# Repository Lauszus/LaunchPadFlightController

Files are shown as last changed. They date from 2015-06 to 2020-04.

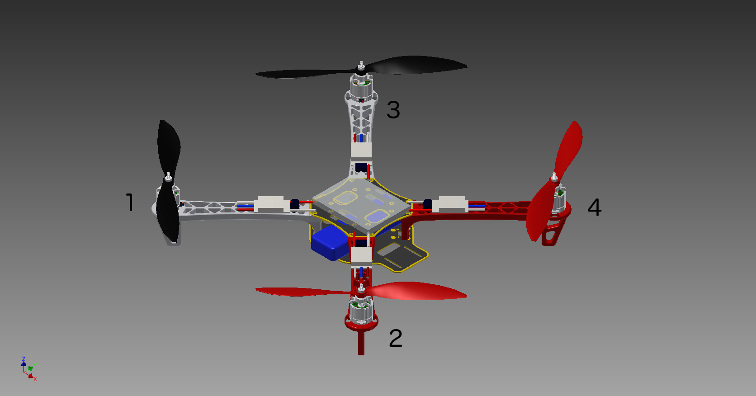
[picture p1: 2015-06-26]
docs/CD-ROM/3D_Model/Renderings/Quad_3d_overview.png

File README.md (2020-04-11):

# LaunchPad Flight Controller
#### Developed by Kristian Sloth Lauszus, 2015-2020
_________


This is a flight controller used for a quadcopter in X-configuration.

It is written for the [Tiva C Series TM4C123G LaunchPad](http://www.ti.com/tool/EK-TM4C123GXL) running at 80 MHz.

More information can be found at the following blog posts: <http://blog.tkjelectronics.dk/2015/01/launchpad-flight-controller> and <http://blog.tkjelectronics.dk/2015/08/bachelors-thesis-launchpad-flight-controller>.

# Video demonstrations

Some video demonstrations of the flight controller can be seen at my [YouTube channel](https://www.youtube.com/playlist?list=PLRBI0ZWd8RfBnD1IZzrBdREjrzRAjWMqg).



# Report

The report I wrote for my Bachelor's thesis can be found in the [docs](docs) folder. The 3D model and Matlab code can be found in there as well.

# Features

* Rate mode, self level mode, heading hold and altitude hold
    - __AUX1:__ Use 3-POS switch for self level and heading hold. At first position both are off, at second position self level is on and at third position both are on
    - __AUX2:__ Use a 3-POS switch for altitude hold. Note that self level mode must be activated for altitude hold to work! At first position altitude hold is turned off, at second position altitude hold will use the distance measured using the sonar and/or LIDAR-Lite v3 and at the third position altitude hold will be using the altitude estimated using the barometer and accelerometer
* Store PID values, calibration values etc. in EEPROM
* Gyro, accelerometer & magnetometer calibration routine
    - Gyro is calibrated at startup
    - Accelerometer and magnetometer calibration routine can be activated in the code or by using the Android app
    - The magnetometer turns on the Blue LED while calibrating
        + Rotate flight controller slowly along all three axis
* Arm/disarm using rudder
* Status LEDs
* Supports CPPM receivers
* Gyro & accelerometer (MPU-6500 or MPU-9250)
* Magnetometer (HMC5883L or AK8963 (inside MPU-9250))
* Barometer (BMP180)
* Ultrasound sensor aka sonar (HC-SR04)
* [LIDAR-Lite v3](https://buy.garmin.com/en-US/US/p/557294)
    - Connect a 680 µF electrolytic capacitor from 5V to GND
* Optical flow sensor (ADNS3080)
* [Android application](https://github.com/Lauszus/LaunchPadFlightControllerAndroid)
* OneShot125 ESC support
* Buzzer feedback

# Current setup

* Motors: Dualsky 980kv
* ESC's: [Hobby King 20A ESC 3A UBEC (F-20A)](http://hobbyking.com/hobbyking/store/uh_viewItem.asp?idProduct=37253) - flashed with SimonK bs_nfet with OneShot125 and COMP_PWM = 1
* Propellers: 10x4.5
* Frame: [Hobby King Q450 V3 Glass Fiber Quadcopter Frame 450mm](http://hobbyking.com/hobbyking/store/__49725__Q450_V3_Glass_Fiber_Quadcopter_Frame_450mm_Integrated_PCB_Version.html)
* LiPo: [Turnigy 3300mAh 3S 30C Lipo Pack](http://hobbyking.com/hobbyking/store/uh_viewItem.asp?idProduct=35870)
* RX: [OrangeRX R615X](http://www.hobbyking.com/hobbyking/store/__46632__OrangeRx_R615X_Spektrum_JR_DSM2_DSMX_Compatible_6Ch_2_4GHz_Receiver_w_CPPM.html)
* TX: [Turnigy 9XR](http://www.hobbyking.com/hobbyking/store/__31544__Turnigy_9XR_Transmitter_Mode_2_No_Module_.html) flashed with OpenTX
* TX module: [OrangeRX 2.4GHz transmitter module](http://hobbyking.com/hobbyking/store/__24656__OrangeRX_DSMX_DSM2_2_4Ghz_Transmitter_Module_JR_Turnigy_compatible_.html)

# Pinout

| Pin  | Connection | Hardware peripheral |
|---|---|---|
| PA0  | UART RX | U0RX (UART0 RX) |
| PA1  | UART TX | U0TX (UART0 TX) |
| PA2  | SPI CLK | SSI0CLK |
| PA3  | SPI SS | SSI0Fss |
| PA4  | SPI MISO | SSI0Rx |
| PA5  | SPI MOSI | SSI0Tx |
| PA6  | SCL | I2C1SCL |
| PA7  | SDA | I2C1SDA |
| PB0* | Bluetooth RX | U1RX (UART1 RX) |
| PB1* | Bluetooth TX | U1TX (UART1 TX) |
| PB4  | Motor 3 | M0PWM2 |
| PB5  | Motor 4 | M0PWM3 |
| PB6  | Motor 1 | M0PWM0 |
| PB7  | Motor 2 | M0PWM1 |
| PC5  | Sonar echo | WTimer0B (WT0CCP1) |
| PC6  | CPPM input | WTimer1A (WT1CCP0) |
| PD2  | Buzzer | |
| PE0  | Sonar trigger | |
| PE1  | ADNS3080 reset | |
| PE2  |  MPU-6500/MPU-9250 INT  | |
| PE3  | HMC5883L DRDY | |
| PF0  | Switch 1 | |
| PF1  | Red LED | |
| PF2  | Blue LED | |
| PF3  | Green LED | |
| PF4  | Switch 2 | |

\* UART1 is connected to an HC-06 Bluetooth module running at a baudrate of 115200. __Not 5V tolerant!__, so make sure your Bluetooth module outputs 3.3 voltage level or use a logic level converter.

Furthermore WTimer1B is used to turn off motors if the connection to the RX is lost. SysTick counter is used for time basic time keeping functionality.

The MPU-6500/MPU-9250, HMC5883L, BMP180 and LIDAR-Lite v3 are connected via I<sup>2</sup>C if they are used.

All pins are defined in [src/Config.h](src/Config.h) and can be overriden by creating a file called "Config_custom.h" in the [src](src) directory allowing you to redefine the values.

# Notes

The motor layout follows the Naze32 in x-configuration i.e. motor 1 is bottom right, motor 2 is top right, motor 3 is bottom left and motor 4 is top left when looking from the back. Motor 1 and 4 should be spinning clockwise and motor 2 and 3 should be spinning counterclockwise.

Make sure that roll increases when tilting quadcopter to the right, pitch increases when pitching quadcopter upward and yaw increases when rotation quadcopter clockwise. This can be displayed using the graph menu in the [Android application](https://github.com/Lauszus/LaunchPadFlightControllerAndroid).

The flight controller is armed by having the throttle low and the rudder to the right. The flight controller is disarmed again by having the throttle low and the rudder to the left.

## Initial setup

1. Locate the line ```#define ONESHOT125 1``` in [PPM.c](src/PPM.c) and set line to 0 if your ESCs does not support OneShot125, if you are in doubt, then set the value to 0.
2. Configure the orientation of the MPU-9250/6500 and HMC5883L, so they corresponds to your setup. This is done inside ```mpu6500BoardOrientation``` and ```hmc5883lBoardOrientation``` in [MPU6500.c](src/MPU6500.c) and [HMC5883L.c](src/HMC5883L.c) respectively.
    * The x-axis should be facing forward, the y-axis should be facing to the right and the z-axis should be facing downward. Typically the axis is indicated on the breakout board for the sensor.

### Calibrating the ESCs

__WARNING:__ Take propellers OFF when testing and calibrating ESCs!!

In order calibrate the ESCs you need to do the following procedure:

1. Power up the board while holding down both hardware switches. The blue LED will come on, indicating that the ESCs will be calibrated at next power up.
2. Turn the board off by disconnecting the battery.
3. Now apply power while holding down the two hardware switches. The board will send out the maximum and minimum pulses to the ESCs and thus calibrating them. When the ESC calibration is done the blue LED will be turned off and a long beep will be played.

The calibration is canceled if the buttons are not held down during the whole procedure or the reset is not performed by a power on reset. The former allows the user to cancel the calibration at any time by releasing the switches and the latter prevents the user from accidentally resetting the board without also resetting the ESCs, for instance by pressing the reset button on the board.

### Calibrating accelerometer and magnetometer

The last step is to calibrate the accelerometer and magnetometer. The accelerometer is calibrated by putting the quadcopter horizontal and activating the calibration routine via the [Android application's](https://github.com/Lauszus/LaunchPadFlightControllerAndroid) settings menu. It is important that the quadcopter is kept still while running the accelerometer calibration routine. When the calibration is done a long beep will be played using the onboard buzzer.

The magnetometer calibration routine is activated similar to the accelerometer by using the [Android application](https://github.com/Lauszus/LaunchPadFlightControllerAndroid). The blue LED will turn on, indicating that the calibration procedure is activated. Now rotate the quadcopter along all three axis slowly in order to find the minimum and maximum values. The user has 30 seconds to rotate the quadcopter. Once the calibration is done the blue LED will be turned off and a long beep will be played.

It is a good idea to confirm that the estimated angles are all correct by using the graph menu in the [Android application](https://github.com/Lauszus/LaunchPadFlightControllerAndroid).

There is no need to calibrate the gyroscope, as this is done at every startup.

### RX

The minimum and maximum receiver values are hardcoded in [src/Config.h](src/Config.h) and might need to be adjusted as well.

# Android application



The Android source code is available at the following repository: <https://github.com/Lauszus/LaunchPadFlightControllerAndroid>.



# GUI

A simple GUI can be found inside the [GUI](GUI) directory. It can be used to visualise the orientation of the flight controller.

# Build instructions

## PlatformIO

[PlatformIO](http://platformio.org) is a cross-platform build system, which makes it easy to compile and upload the code on both Windows, Linux and Mac. This is the recommended way to compile the code for novice users.

Please follow these instructions in order to install Python 2.7 and PlatformIO: <http://docs.platformio.org/en/latest/installation.html>.

On Windows be sure to select "Add python.exe to Path" when installing Python 2.7.

Open a terminal (search for ```cmd.exe``` on Windows) and navigate to the root of the project:

```bash
cd LaunchPadFlightController
```

Now compile the code:

```bash
platformio run
```

The program should now be compiled.

In order to upload the code simply type:

```bash
platformio run -t upload
```

I recommend installing the [PlatformIO IDE](http://platformio.org/get-started/ide?install) if using PlatformIO.

## Keil µVision IDE 5

In order to built this project you need to download Keil µVision IDE 5 and then simply open the [project file](LaunchPadFlightController.uvprojx).

## Manual installation

In order to built this project you will need to use [Make](http://www.gnu.org/software/make/).

First download and install [gcc-arm-none-eabi](https://launchpad.net/gcc-arm-embedded/4.8/4.8-2014-q3-update) and then install [lm4tools](https://github.com/utzig/lm4tools).

lm4tools can be installed like so:

```bash
$ git clone https://github.com/utzig/lm4tools.git
$ make -C lm4tools/lm4flash all
$ sudo cp lm4tools/lm4flash/lm4flash /usr/bin/
```

If you are on a Mac, I recommend installing gcc-arm-none-eabi using [Homebrew](http://brew.sh) like so:

```bash
$ brew tap PX4/homebrew-px4
$ brew update
$ brew install gcc-arm-none-eabi
```

Now simply compile the code by navigating to the [src](src) and running the following command:

```bash
make
```

And to upload the code:

```bash
make flash
```

Some information on configuring Eclipse for use with this project can be the [Wiki](https://github.com/Lauszus/LaunchPadFlightController/wiki).

### Hardware debugging using OpenOCD

OpenOCD can be installed via [Homebrew](http://brew.sh) as well:

```bash
$ brew install openocd
```

Now run the following commands:

```bash
$ openocd --file /usr/local/share/openocd/scripts/board/ek-tm4c123gxl.cfg

$ arm-none-eabi-gdb gcc/LaunchPadFlightController.axf
(gdb) target extended-remote :3333
(gdb) monitor reset halt
(gdb) load
(gdb) monitor reset init
```

More information regarding hardware debugging can be found at the [Wiki](https://github.com/Lauszus/LaunchPadFlightController/wiki/Hardware-Debugging-In-Eclipse).

# Credits

A lot of the inspiration for this code came from [Cleanflight](https://github.com/cleanflight/cleanflight) and other open source flight controller projects.

For more information send me an email at <lauszus@gmail.com>.

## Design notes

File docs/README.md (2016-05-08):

# LaunchPad Flight Controller
#### Developed by Kristian Sloth Lauszus, 2015
_________

This is the report I wrote for my bachelor thesis including the appendix I attached as a [CD-ROM](CD-ROM).

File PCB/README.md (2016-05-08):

# LaunchPad Flight Controller
#### Developed by Kristian Sloth Lauszus, 2015
_________

This is the design files for the PCB that is designed to plug onto the headers on the Tiva LaunchPad. You can order the PCB directly from the following link: <https://www.oshpark.com/shared_projects/9DC5cp8e>.

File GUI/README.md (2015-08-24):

#### Developed by Kristian Sloth Lauszus, 2015

The code is released under the GNU General Public License.
_________

This is a [Processing](http://processing.org/) application I made to visualize the orientation of the flight controller.

For more information send me an email at <lauszus@gmail.com>.

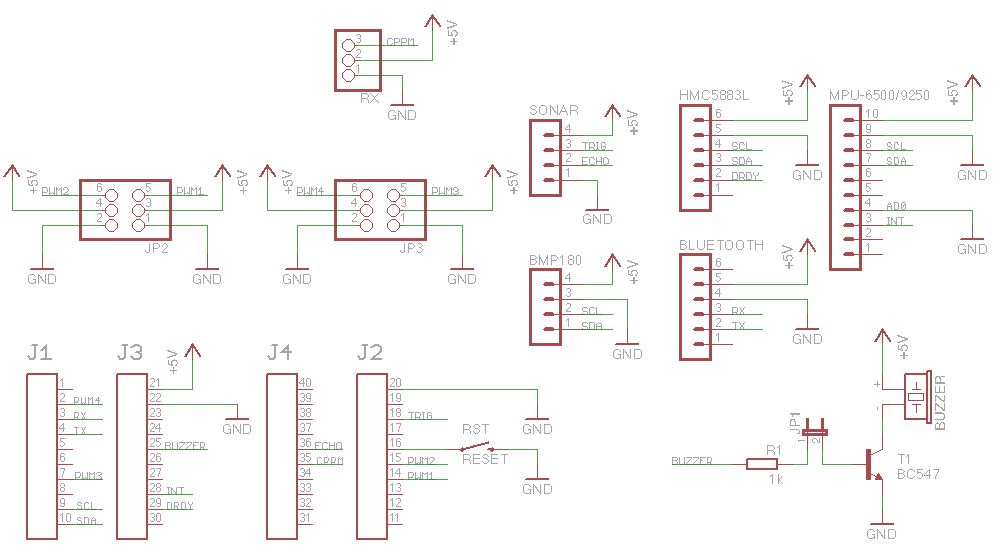
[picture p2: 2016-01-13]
PCB/LaunchPadFlightController_Schematic.png

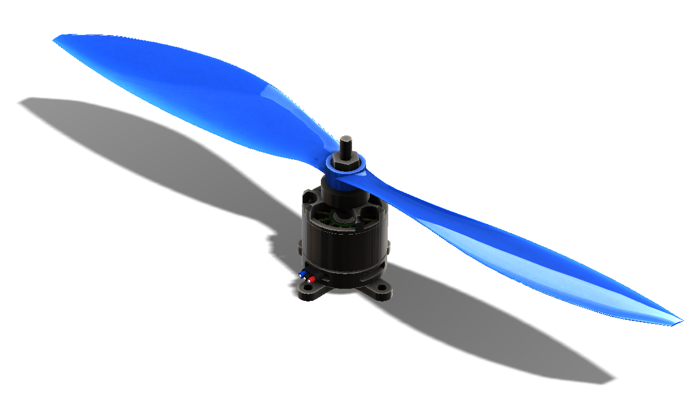
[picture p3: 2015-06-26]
docs/CD-ROM/3D_Model/Motor/Renderings/Iso_w_Prop.png

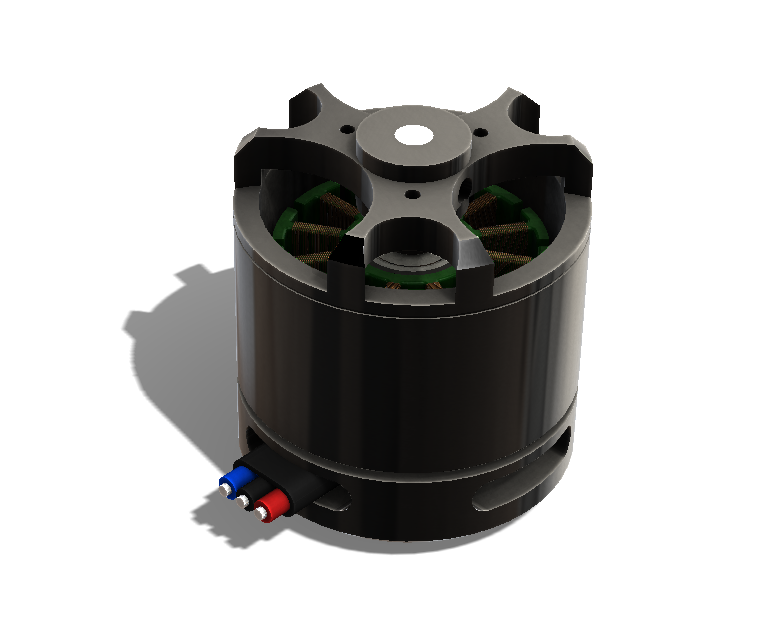
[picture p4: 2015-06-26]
docs/CD-ROM/3D_Model/Motor/Renderings/Iso_wo_Caps.png

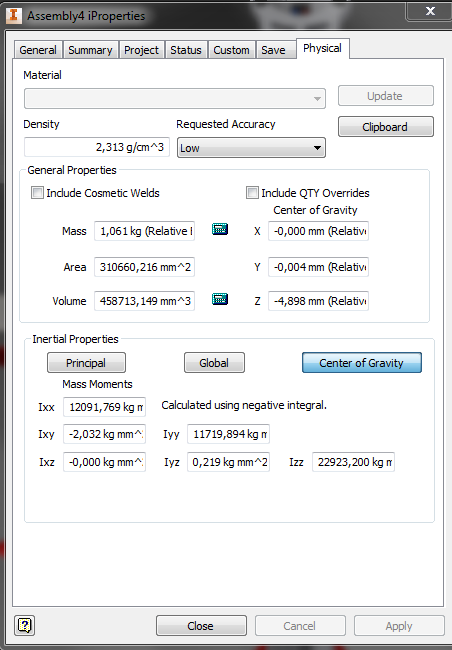
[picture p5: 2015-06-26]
docs/CD-ROM/3D_Model/moment_of_inertia.png

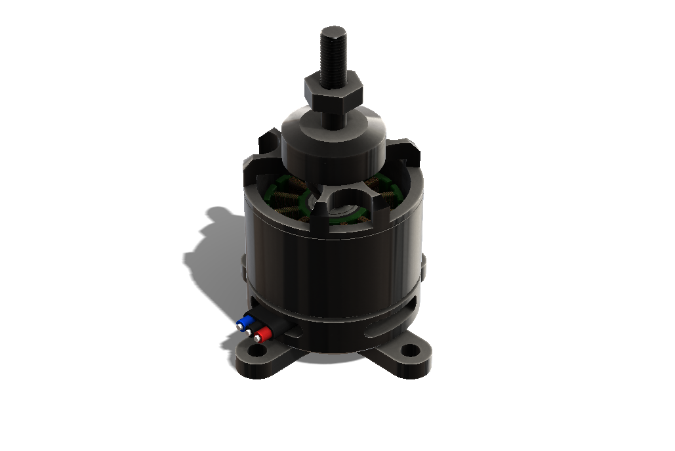
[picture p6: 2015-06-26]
docs/CD-ROM/3D_Model/Motor/Renderings/Iso_w_Caps.png

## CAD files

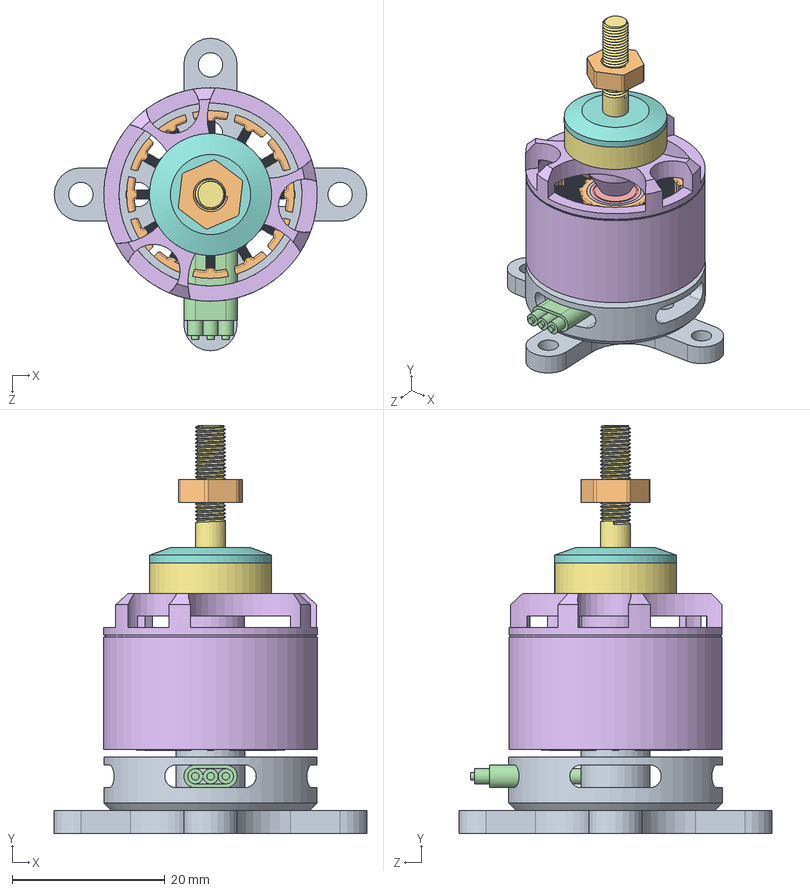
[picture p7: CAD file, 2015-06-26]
docs/CD-ROM/3D_Model/Motor/Assemblies/Motor_wo_Prop.SLDASM
41.0 x 53.5 x 41.0 mm
Housing_Bottom
Stator_Steelcore
Stator_Coil x 12
Wiring
Rotor
Housing_Upper
CapScrew
Cap
CrossBase
Nut

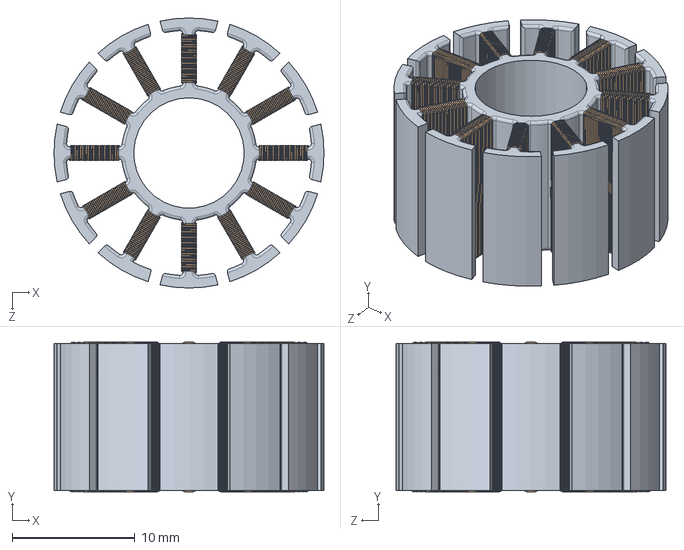
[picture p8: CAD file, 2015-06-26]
docs/CD-ROM/3D_Model/Motor/Assemblies/Stator.SLDASM
22.0 x 12.2 x 22.0 mm
Stator_Steelcore
Stator_Coil x 12

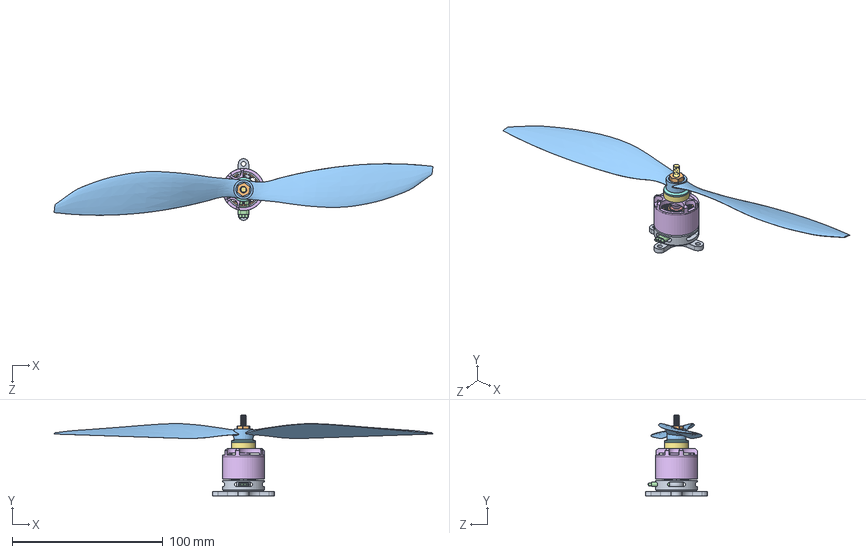
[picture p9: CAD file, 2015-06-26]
docs/CD-ROM/3D_Model/Motor/Assemblies/Motor_w_Prop.SLDASM
251.7 x 53.5 x 41.0 mm
Housing_Bottom
Stator_Steelcore
Stator_Coil x 12
Wiring
Rotor
Housing_Upper
CapScrew
Cap
CrossBase
Nut
1047CCW

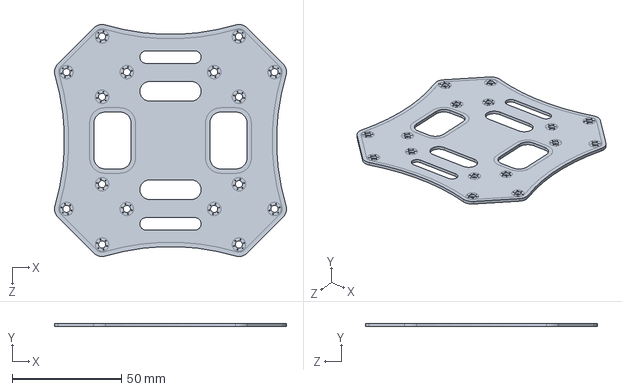
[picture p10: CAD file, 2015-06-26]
docs/CD-ROM/3D_Model/F450 Top Plate.SLDPRT
106.1 x 1.52 x 106.1 mm

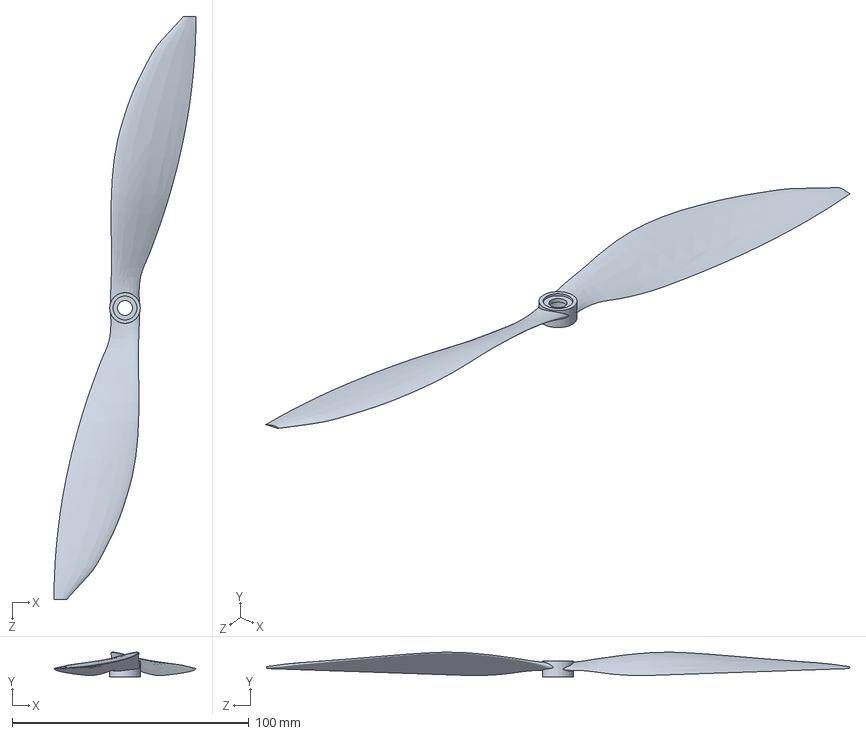
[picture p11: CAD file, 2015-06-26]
docs/CD-ROM/3D_Model/Motor/Assemblies/10x4.7-counterclockwise-propeller.SLDPRT
60.0 x 10.5 x 246.4 mm

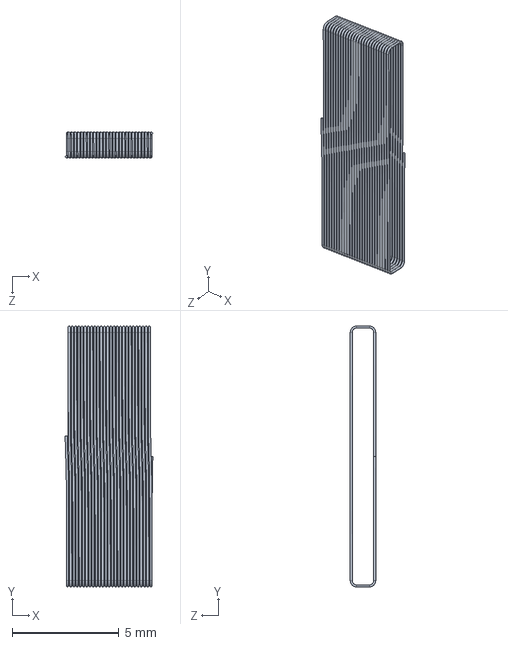
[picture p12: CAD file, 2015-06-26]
docs/CD-ROM/3D_Model/Motor/Parts/Stator_Coil.SLDPRT
4.10 x 12.2 x 1.20 mm

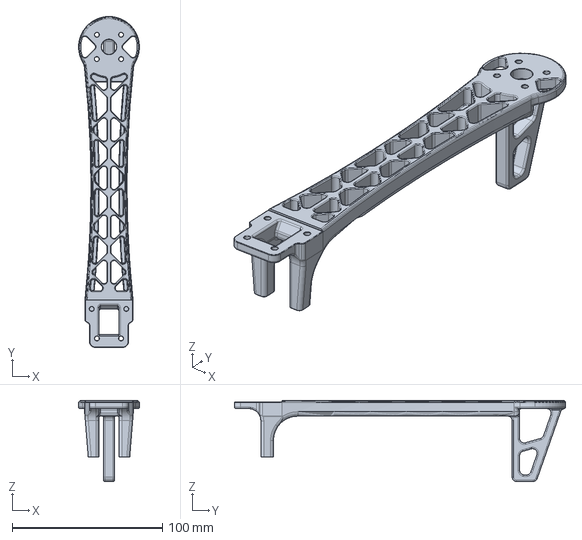
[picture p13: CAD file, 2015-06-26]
docs/CD-ROM/3D_Model/F450 arm.stp
40.5 x 220.2 x 54.0 mm

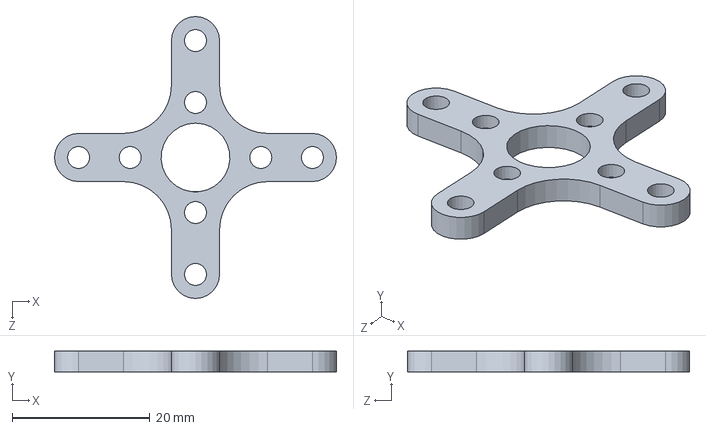
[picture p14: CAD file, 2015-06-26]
docs/CD-ROM/3D_Model/Motor/Parts/CrossBase.SLDPRT
41.0 x 3.00 x 41.0 mm

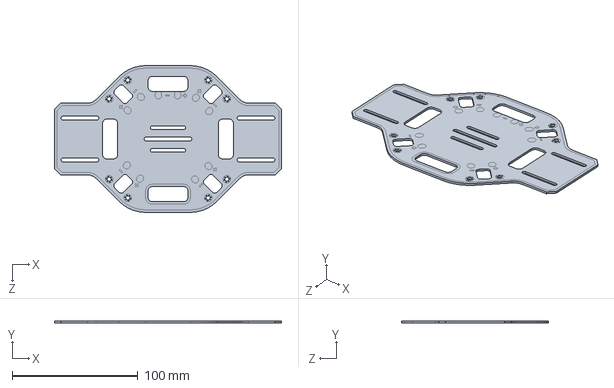
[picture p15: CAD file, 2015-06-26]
docs/CD-ROM/3D_Model/F450 chasis.SLDPRT
180.5 x 1.52 x 116.8 mm

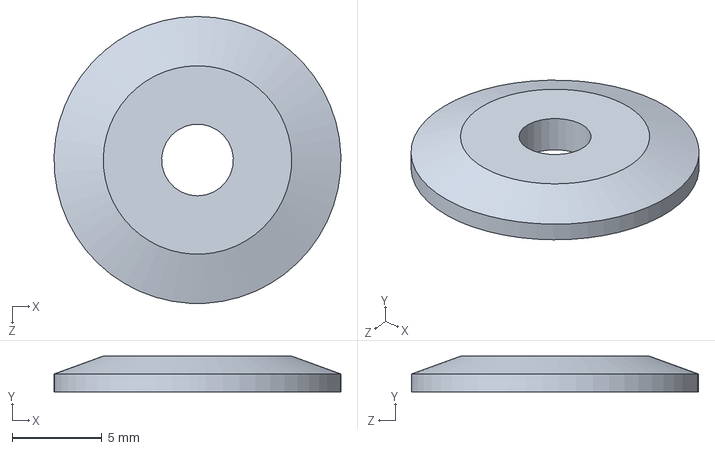
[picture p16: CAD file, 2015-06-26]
docs/CD-ROM/3D_Model/Motor/Parts/Cap.SLDPRT
16.0 x 2.00 x 16.0 mm

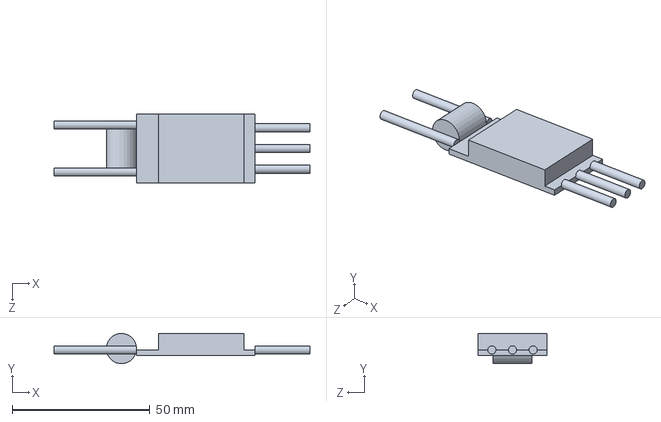
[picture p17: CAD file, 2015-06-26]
docs/CD-ROM/3D_Model/Motor/Assemblies/Hobby King 20A ESC 3A UBEC.SLDPRT
93.0 x 11.0 x 25.0 mm

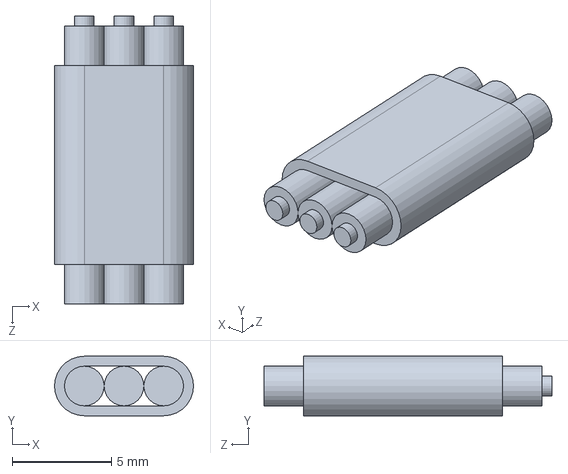
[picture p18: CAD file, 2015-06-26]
docs/CD-ROM/3D_Model/Motor/Parts/Wiring.SLDPRT
7.00 x 3.00 x 14.5 mm

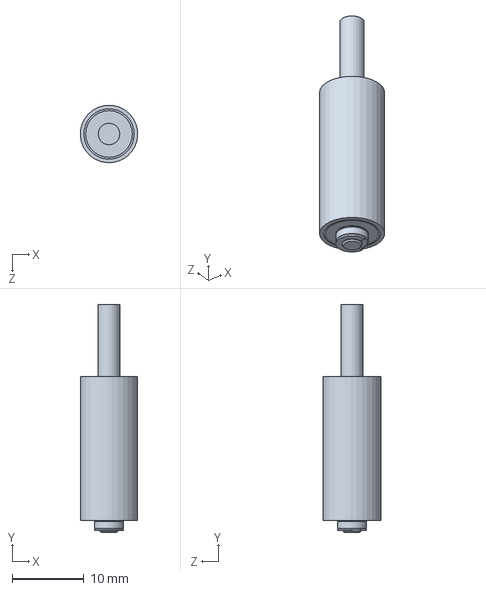
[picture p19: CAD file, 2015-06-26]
docs/CD-ROM/3D_Model/Motor/Parts/Rotor.SLDPRT
7.99 x 31.7 x 8.00 mm

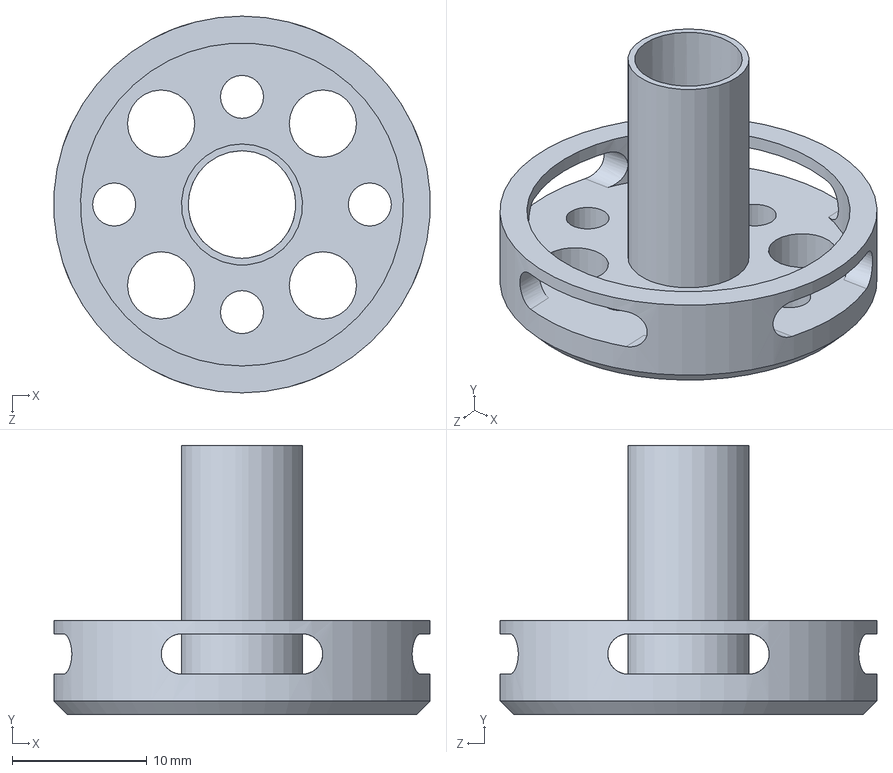
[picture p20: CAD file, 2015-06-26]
docs/CD-ROM/3D_Model/Motor/Parts/Housing_Bottom.SLDPRT
27.9 x 20.0 x 28.0 mm

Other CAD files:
docs/CD-ROM/3D_Model/Motor/Assemblies/SunnySky X2212_13_980kV.SLDASM
docs/CD-ROM/3D_Model/Motor/Assemblies/10x4.7-clockwise-propeller.SLDPRT
docs/CD-ROM/3D_Model/Motor/Parts/Housing_Upper.SLDPRT
docs/CD-ROM/3D_Model/Motor/Parts/Stator_Steelcore.SLDPRT
docs/CD-ROM/3D_Model/Batteri.ipt
docs/CD-ROM/3D_Model/F450 arm.ipt
docs/CD-ROM/3D_Model/Flight controller.ipt
docs/CD-ROM/3D_Model/Imported Components/F450 Top Plate/F450 Top Plate.ipt
docs/CD-ROM/3D_Model/Imported Components/F450 Top Plate/OldVersions/F450 Top Plate.0002.ipt
docs/CD-ROM/3D_Model/Imported Components/F450 chasis/F450 chasis.ipt
docs/CD-ROM/3D_Model/Imported Components/F450 chasis/OldVersions/F450 chasis.0002.ipt
docs/CD-ROM/3D_Model/Motor/Assemblies/Imported Components/10x4.7-clockwise-propeller/10x4.7-clockwise-propeller.ipt
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

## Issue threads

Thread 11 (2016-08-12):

Port to TM4c129x

PAk-CatchFire, 2016-08-12:
Hello,
first of all....excellent work.

Will you port it to latest TM4c129x Tivaware family?
Regards.

Lauszus, 2016-08-12:
Thanks :)
No I am not currently planning on it, but if you want to you are more than welcome to do so.

PAk-CatchFire, 2016-09-22:
Thanks @Lauszus. Finally I was able to port it for 129X and 123X devices. But unfortunatelly, the yaw, raw and theta I am getting are not correct.

Would you mind to take a look on it? All the code is on my Github

https://github.com/PAk-CatchFire/MPU9250-Tivaware

Regards

Lauszus, 2016-09-23:
@PAk-CatchFire what exactly do you want me to look at? If you want to use the driver for the MPU-9250, then you can just use mine. But you will have to change the I2C driver for the TM4C129x family: https://github.com/Lauszus/LaunchPadFlightController/blob/master/src/I2C.c.

Lauszus, 2016-09-23:
Btw the TM4c129x family is not the "latest family", but simply a different family, which purpose if you want to use it for IoT etc.

PAk-CatchFire, 2016-09-28:
Ok, the129x  I2C driver is one part I already implemented.

In which file is located your MPU-9250 driver? Is it spreaded through some files?

Thanks

Lauszus, 2016-09-28:
As the MPU-9250 is the same sensor as the MPU-6500, but just with a AK8963 magnetometer inside. I simply use the MPU-6500 driver: https://github.com/Lauszus/LaunchPadFlightController/blob/master/src/MPU6500.c and then a dedicated driver for the magnetometer: https://github.com/Lauszus/LaunchPadFlightController/blob/master/src/AK8963.c.

Here is the commit that added support for the MPU-9250: https://github.com/Lauszus/LaunchPadFlightController/commit/527d39360ec56c56bb9e7cf42679e29b8ef919eb.

You shouldn't have to modify the driver in any way, as I use the TivaWare librayr: https://github.com/Lauszus/LaunchPadFlightController/tree/master/lib. The part is then simply set in the Makefile: https://github.com/Lauszus/LaunchPadFlightController/blob/master/src/Makefile#L28.

You might want to use different pins for the I2C interface: https://github.com/Lauszus/LaunchPadFlightController/blob/master/src/I2C.c, that is all you might have to change.

PAk-CatchFire, 2016-09-28:
Thank you Lauszus, I was checking your drivers and they work fine for the accelerometer & gyro part, however the magnetometer gets stuck reading 0 values. So i used the function in my code:
https://github.com/PAk-CatchFire/MPU9250-Tivaware/blob/master/PAk_MPU9250_Tivaware/MPU9250/MPU9250.c#L472

I have improved my readings because I had some error on the scale, however my result is jittering (probably the filter is not good enough).

I haven't seen that you use any of the traditional Madgwick/Mahony QuaternionUpdate....are you using your own? Is it worth it?

Best Regards

Lauszus, 2016-10-10:
I am just using a complimentary filter: https://github.com/Lauszus/LaunchPadFlightController/blob/master/src/IMU.c.

Closed 2017-03-25.

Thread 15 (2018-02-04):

buzzer.c

mtayyip, 2018-02-04:
Hi,
in the buzzer code :
GPIOPinTypeGPIOOutput(GPIO_BUZZER_BASE, GPIO_PIN_BUZZER);
it's running all the time buzzer.

And this code:
GPIOPinWrite(GPIO_BUZZER_BASE, GPIO_PIN_BUZZER, enable ? GPIO_PIN_BUZZER : 0);//enable is false
continues to work, does not stop

moisesesc, 2018-02-04:
Could be the hardware... Shorted buzzer driver

On Feb 4, 2018 8:07 AM, Muhammet Tayyip Çankaya <notifications@github.com> wrote:

Hi,
in the buzzer code :
GPIOPinTypeGPIOOutput(GPIO_BUZZER_BASE, GPIO_PIN_BUZZER);
it's running all the time buzzer.

And this code:
GPIOPinWrite(GPIO_BUZZER_BASE, GPIO_PIN_BUZZER, enable ? GPIO_PIN_BUZZER : 0);//enable is false
continues to work, does not stop

—
You are receiving this because you are subscribed to this thread.
Reply to this email directly, view it on GitHub<https://github.com/Lauszus/LaunchPadFlightController/issues/15>, or mute the thread<https://github.com/notifications/unsubscribe-auth/AA0qHfhMlDMLPutnG8nd9ZTVwRsZwCHBks5tRauHgaJpZM4R4j83>.

mtayyip, 2018-02-04:
I connected the vcc to 3.3 volts.now it is OK

Lauszus, 2018-02-04:
@mtayyip good to hear you got it working :)

Closed 2018-02-04.

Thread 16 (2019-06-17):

What's the LED status means?

MrThanlon, 2019-06-17:
- green?
- red?

Lauszus, 2019-06-17:
The RED LED indicates that the flight controller is armed and the green indicates that it is unarmed. The blue LED has different meanings, please read the README for more information: https://github.com/Lauszus/LaunchPadFlightController#launchpad-flight-controller.

Lauszus, 2019-06-20:
I'm closing this issue, as I believe it is solved. Please reopen if needed :)

Closed 2019-06-20.

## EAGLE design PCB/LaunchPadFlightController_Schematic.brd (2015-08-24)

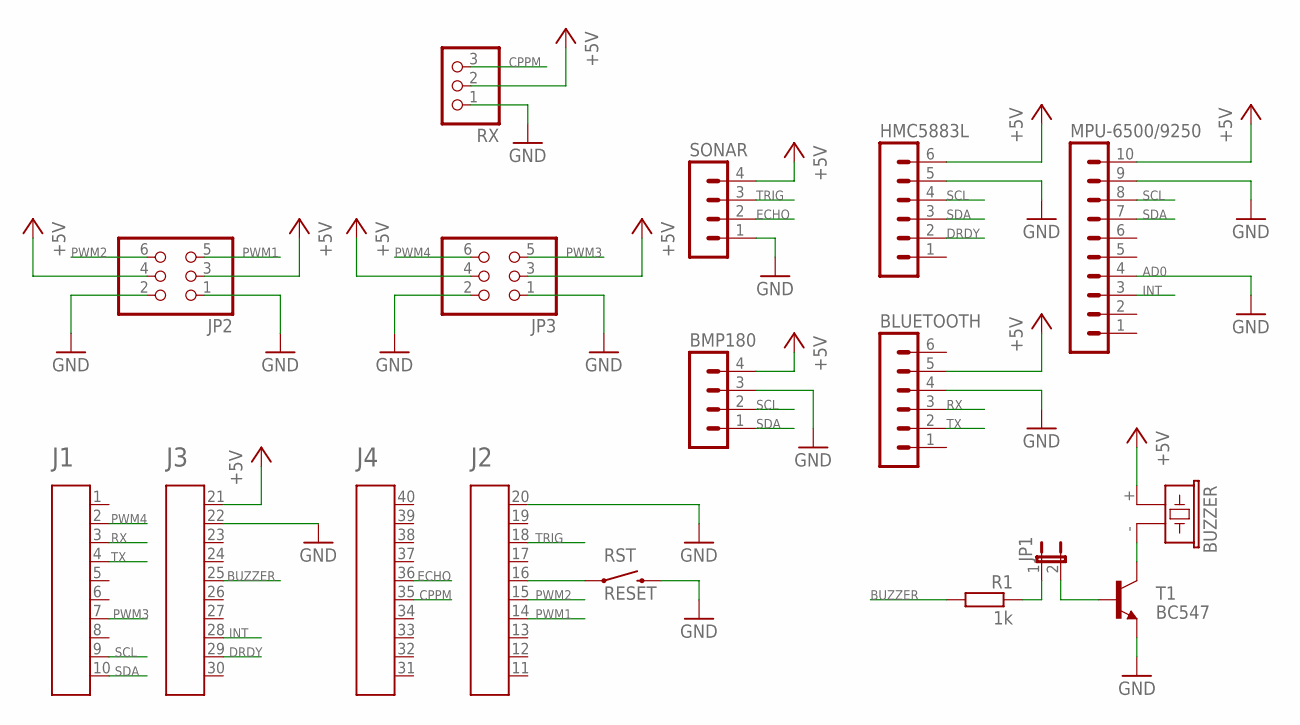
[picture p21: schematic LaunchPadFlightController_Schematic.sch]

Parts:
A1: HEADER4X10-BOOSTERPACK; 4X10-BOOSTERPACK
BLUETOOTH: MA06-1
BMP180: MA04-1
BUZZER: F/CM12P
HMC5883L: MA06-1
JP1: JP1E; JP1
JP2, JP3: PINHD-2X3; 2X03
MPU-6500/9250: MA10-1
R1: 1k; 0207/10
RST: RESET; TACTILE-PTH-EZ
RX: PINHD-1X3; 1X03
SONAR: MA04-1
T1: BC547; TO92

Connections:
+5V: A1.21, BLUETOOTH.5, BMP180.4, BUZZER.+ (1), HMC5883L.6, JP2.3, JP2.4, JP3.3, JP3.4, MPU-6500/9250.10, RX.2, SONAR.4
BUZZER: A1.25, R1.2
CPPM: A1.35, RX.3
DRDY: A1.29, HMC5883L.2
ECHO: A1.36, SONAR.2
GND: A1.20, A1.22, BLUETOOTH.4, BMP180.3, HMC5883L.5, JP2.1, JP2.2, JP3.1, JP3.2, MPU-6500/9250.4, MPU-6500/9250.9, RST.3 (2), RX.1, SONAR.1, T1.1 (E)
INT: A1.28, MPU-6500/9250.3
unnamed: A1.16, RST.1
unnamed: JP1.1, R1.1
unnamed: JP1.2, T1.2 (B)
unnamed: BUZZER.- (2), T1.3 (C)
PWM1: A1.14, JP2.5
PWM2: A1.15, JP2.6
PWM3: A1.7, JP3.5
PWM4: A1.2, JP3.6
RX: A1.3, BLUETOOTH.3
SCL: A1.9, BMP180.2, HMC5883L.4, MPU-6500/9250.8
SDA: A1.10, BMP180.1, HMC5883L.3, MPU-6500/9250.7
TRIG: A1.18, SONAR.3
TX: A1.4, BLUETOOTH.2

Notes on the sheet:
AD0

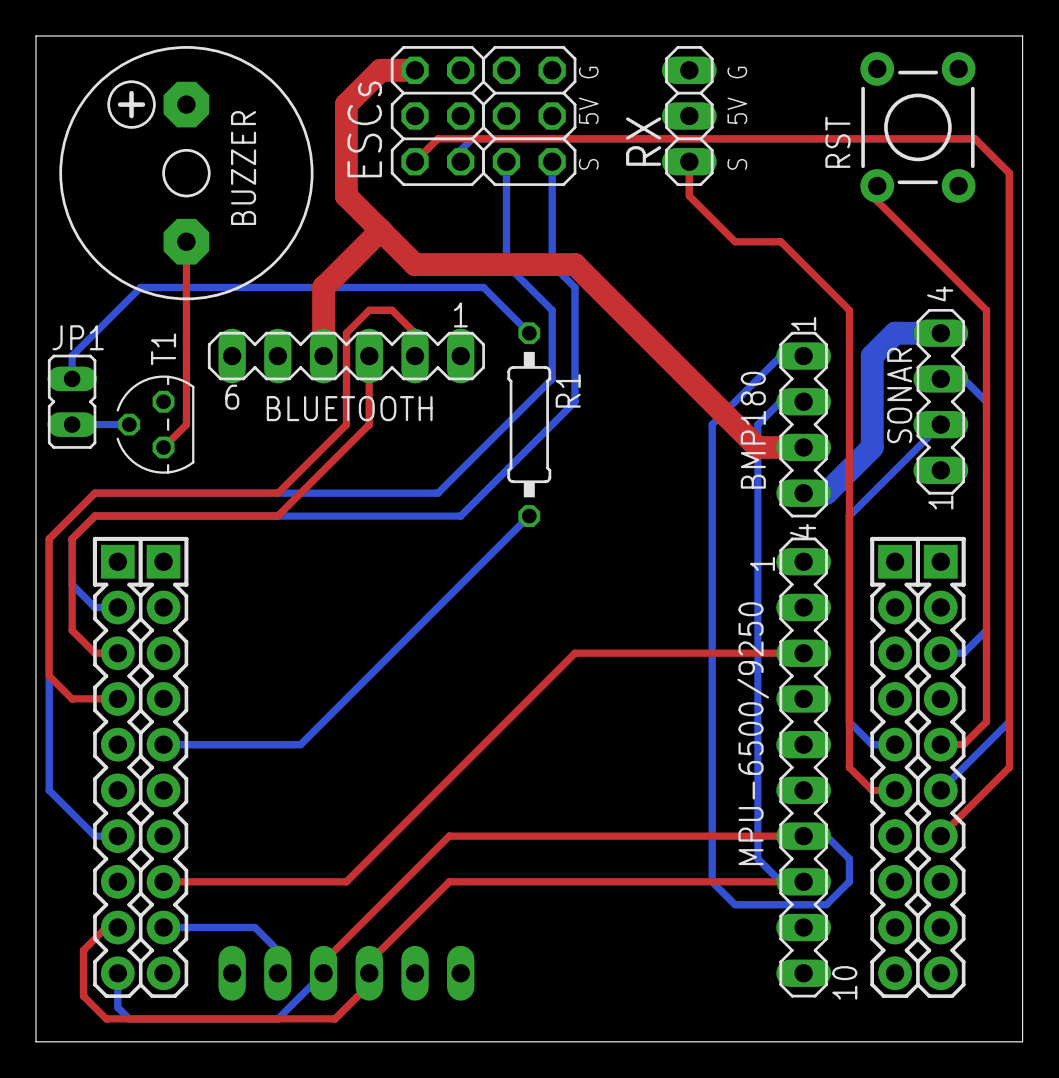
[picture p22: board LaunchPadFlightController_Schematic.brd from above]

Board: 2 copper layers, 54.8 x 55.9 mm, 14 parts (1 on the bottom side), 20 nets.

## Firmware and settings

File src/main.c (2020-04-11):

/* Copyright (C) 2015 Kristian Sloth Lauszus. All rights reserved.

 This software may be distributed and modified under the terms of the GNU
 General Public License version 2 (GPL2) as published by the Free Software
 Foundation and appearing in the file GPL2.TXT included in the packaging of
 this file. Please note that GPL2 Section 2[b] requires that all works based
 on this software must also be made publicly available under the terms of
 the GPL2 ("Copyleft").

 Contact information
 -------------------

 Kristian Sloth Lauszus
 Web      :  http://www.lauszus.com
 e-mail   :  lauszus@gmail.com
*/

#include <stdint.h>
#include <stdbool.h>
#include <math.h>

#include "AltitudeHold.h"
#include "ADNS3080.h"
#include "Bluetooth.h"
#include "Buzzer.h"
#include "Config.h"
#include "EEPROM.h"
#include "HeadingHold.h"
#include "I2C.h"
#include "IMU.h"
#include "Magnetometer.h"
#include "MPU6500.h"
#include "PPM.h"
#include "PID.h"
#include "RX.h"
#include "SPI.h"
#include "StepResponse.h"
#include "Time.h"
#include "UART.h"

#include "inc/hw_memmap.h"
#include "driverlib/gpio.h"
#include "driverlib/interrupt.h"
#include "driverlib/sysctl.h"
#if UART_DEBUG
#include "utils/uartstdio.h" // Add "UART_BUFFERED" to preprocessor
#endif

static angle_t angle; // Struct used to store angles
static mpu6500_t mpu6500; // Gyro and accelerometer readings
static sensor_t mag = { .data = { 1.0f, 0.0f, 0.0f } }; // If no magnetometer is used, then just use a vector with a x-component only

int main(void) {
    // Set the clocking to run directly from the external crystal/oscillator and use PLL to run at 80 MHz
    SysCtlClockSet(SYSCTL_SYSDIV_2_5 | SYSCTL_USE_PLL | SYSCTL_OSC_MAIN | SYSCTL_XTAL_16MHZ); // Set clock to 80 MHz (400 MHz(PLL) / 2 / 2.5 = 80 MHz)

    SysCtlPeripheralEnable(SYSCTL_PERIPH_LED); // Enable peripheral
    SysCtlDelay(2); // Insert a few cycles after enabling the peripheral to allow the clock to be fully activated
    GPIOPinTypeGPIOOutput(GPIO_LED_BASE, GPIO_RED_LED | GPIO_BLUE_LED | GPIO_GREEN_LED); // Set red, blue and green LEDs as outputs

    initPID();
#if UART_DEBUG
    initUART();
#endif
    initTime();
    initBuzzer();
    initEEPROM();
    initPPM();
    initRX();
    initI2C();
    initMPU6500(&mpu6500);
#if USE_MAG
    initMag();
#endif
#if USE_SONAR || USE_BARO || USE_LIDAR_LITE
    initAltitudeHold();
#endif
#if USE_FLOW_SENSOR
    initSPI();
    initADNS3080();
#endif
    initBluetooth();
    IntMasterEnable(); // Enable all interrupts

#if UART_DEBUG
    UARTprintf("Accelerometer zero values: %d\t%d\t%d\n", cfg.accZero.axis.X, cfg.accZero.axis.Y, cfg.accZero.axis.Z);
#endif

#if UART_DEBUG && USE_MAG
    UARTprintf("Magnetometer zero values: %d\t%d\t%d\n", (int16_t)cfg.magZero.axis.X, (int16_t)cfg.magZero.axis.Y, (int16_t)cfg.magZero.axis.Z);
#endif

#if UART_DEBUG
    printPIDValues(pidRoll.values); // Print PID Values
    printPIDValues(pidYaw.values);
    printPIDValues(pidSonarAltHold.values);
    printPIDValues(pidBaroAltHold.values);
    printSettings(); // Print settings
#endif

    while (!validRXData) {
        // Wait until we have valid data
    }

#if UART_DEBUG
    UARTprintf("Ready\n");
#endif
    beepBuzzer(); // Indicate startup

    while (1) {
        // Make sure there is valid data and safety channel is in armed position
        static bool armed = false;
        if (validRXData) {
            if (!armed && getRXChannel(RX_THROTTLE_CHAN) < CHANNEL_MIN_CHECK && getRXChannel(RX_RUDDER_CHAN) > CHANNEL_MAX_CHECK) // Arm using throttle low and yaw right
                armed = true;
            else if (armed && getRXChannel(RX_THROTTLE_CHAN) < CHANNEL_MIN_CHECK && getRXChannel(RX_RUDDER_CHAN) < CHANNEL_MIN_CHECK) // Disarm using throttle low and yaw left
                armed = false;
        } else
            armed = false;

        static bool lastArmed = false;
        if (armed != lastArmed)
            beepBuzzer(); // Indicate that armed status were changed
        lastArmed = armed;

        // Turn on red led if armed otherwise turn on green LED
        GPIOPinWrite(GPIO_LED_BASE, GPIO_RED_LED | GPIO_GREEN_LED, armed ? GPIO_RED_LED : GPIO_GREEN_LED);

        // Handle the different modes
        bool angleMode = getRXChannel(RX_AUX1_CHAN) > -10;
#if USE_MAG
        bool headMode = angleMode && getRXChannel(RX_AUX1_CHAN) > 50; // Make sure angle mode is activated in heading hold mode
#endif
#if USE_SONAR || USE_BARO || USE_LIDAR_LITE
        bool altitudeMode = angleMode && getRXChannel(RX_AUX2_CHAN) > -10; // Make sure angle mode is activated in altitude hold mode
#endif

        // Don't spin motors if the throttle is low
        bool runMotors = false;
        if (armed &&
#if USE_SONAR
                (getRXChannel(RX_THROTTLE_CHAN) > CHANNEL_MIN_CHECK || altitudeMode)) // If in altitude mode using sonar, keep motors spinning anyway
#else
                getRXChannel(RX_THROTTLE_CHAN) > CHANNEL_MIN_CHECK)
#endif
            runMotors = true;
        else if (readBluetoothData(&mpu6500, &angle)) // Read Bluetooth data if motors are not spinning
            beepBuzzer(); // Indicate if new values were set

        if (dataReadyMPU6500()) {
            uint32_t now = micros();
            static uint32_t timer = 0; // Used to keep track of the time
            float dt = (float)(now - timer) / 1e6f; // Convert to seconds
            //UARTprintf("%d\n", now - timer);
            timer = now;

            // Read IMU
            getMPU6500Data(&mpu6500); // Get accelerometer and gyroscope values
#if USE_MAG
            getMagData(&mag, false); // Get magnetometer values with zero values subtracted
#endif
            getAngles(&mpu6500, &mag, &angle, dt); // Calculate pitch, roll and yaw

#if USE_SONAR || USE_BARO || USE_LIDAR_LITE
            static altitude_t altitude;
            getAltitude(&angle, &mpu6500, &altitude, now, dt);
#endif

            /*UARTprintf("%d\t%d\t%d\n", (int16_t)angle.axis.roll, (int16_t)angle.axis.pitch, (int16_t)angle.axis.yaw);
            UARTFlushTx(false);*/

            // Motors routine
            if (runMotors) {
                float aileron = getRXChannel(RX_AILERON_CHAN);
                float elevator = -getRXChannel(RX_ELEVATOR_CHAN); // Invert so it follows the right hand rule for the NED-coordinate system
                float rudder = getRXChannel(RX_RUDDER_CHAN);
                //UARTprintf("%d\t%d\t%d\n", (int16_t)aileron, (int16_t)elevator, (int16_t)rudder);

#if USE_MAG
                if (headMode && fabsf(rudder) < 5) // Only use heading hold if user is not applying rudder
                    rudder = updateHeadingHold(&angle, rudder, now);
                else
                    resetHeadingHold(&angle);
#endif

                float setpointRoll, setpointPitch; // Roll and pitch control can both be gyro or accelerometer based
                const float setpointYaw = rudder * cfg.stickScalingYaw; // Yaw is always gyro controlled
                if (angleMode) { // Angle mode
                    const uint8_t maxAngleInclination =
#if USE_SONAR || USE_LIDAR_LITE
                            altitudeMode ? cfg.maxAngleInclinationDistSensor :
#endif
                            cfg.maxAngleInclination; // If in altitude mode the angle has to be limited to the capability of the sonar

#if STEP_ACRO_SELF_LEVEL
                    static const float step1 = 0; // Start at 0 degrees
                    static const float step2 = 15; // Tilt 15 degrees
                    static const uint32_t interval = 1e6; // 1s between steps
                    aileron = stepResponse(getRXChannel(RX_AUX2_CHAN) > 0, aileron, angle.axis.roll, step1, step2, interval, now);
#endif
                    setpointRoll = constrain(aileron, -maxAngleInclination, maxAngleInclination) - angle.axis.roll;
                    setpointPitch = constrain(elevator, -maxAngleInclination, maxAngleInclination) - angle.axis.pitch;
                    setpointRoll *= cfg.angleKp; // A cascaded P controller is used in self level mode, as the output from the P controller is then used as the set point for the acro PID controller
                    setpointPitch *= cfg.angleKp;
                } else { // Acro mode
                    setpointRoll = aileron * cfg.stickScalingRollPitch;
                    setpointPitch = elevator * cfg.stickScalingRollPitch;

#if STEP_ACRO_SELF_LEVEL
                    static const float step1 = 0; // Start at 0 degrees/s
                    static const float step2 = 15; // Rotate 15 degrees/s
                    static const uint32_t interval = 1e6; // 1s between steps
                    setpointRoll = stepResponse(getRXChannel(RX_AUX2_CHAN) > 0, setpointRoll, mpu6500.gyroRate.axis.roll, step1, step2, interval, now);
#endif
                }

                /*UARTprintf("%d\t%d\n", (int16_t)setpointRoll, (int16_t)setpointPitch);
                UARTFlushTx(false);*/

                float rollOut = updatePID(&pidRoll, setpointRoll, mpu6500.gyroRate.axis.roll, dt);
                float pitchOut = updatePID(&pidPitch, setpointPitch, mpu6500.gyroRate.axis.pitch, dt);
                float yawOut = updatePID(&pidYaw, setpointYaw, mpu6500.gyroRate.axis.yaw, dt);

                float throttle = getRXChannel(RX_THROTTLE_CHAN);

#if USE_SONAR || USE_BARO || USE_LIDAR_LITE
                if (altitudeMode)
                    throttle = updateAltitudeHold(getRXChannel(RX_AUX2_CHAN), &altitude, throttle, now, dt);
                else
                    resetAltitudeHold(&altitude);
#endif

                float motors[4]; // Motor 0 is bottom right, motor 1 is top right, motor 2 is bottom left and motor 3 is top left
                for (uint8_t i = 0; i < 4; i++)
                    motors[i] = throttle;

                // Apply mix for quadcopter in x-configuration
                motors[0] -= rollOut;
                motors[1] -= rollOut;
                motors[2] += rollOut;
                motors[3] += rollOut;

                motors[0] -= pitchOut;
                motors[1] += pitchOut;
                motors[2] -= pitchOut;
                motors[3] += pitchOut;

                motors[0] -= yawOut;
                motors[1] += yawOut;
                motors[2] += yawOut;
                motors[3] -= yawOut;

                updateMotorsAll(motors);

                //UARTprintf("%d\t%d\n", (int16_t)elevator, (int16_t)aileron);
#if 0
                UARTprintf("%d\t%d\t\t", (int16_t)angle.axis.roll, (int16_t)angle.axis.pitch);
                UARTprintf("%d\t%d\t\t", (int16_t)rollOut, (int16_t)pitchOut);
                UARTprintf("%d\t%d\t%d\t%d\n", (int16_t)motors[0], (int16_t)motors[1], (int16_t)motors[2], (int16_t)motors[3]);
                UARTFlushTx(false);
#endif
            } else {
                writePPMAllOff();
                resetPIDRollPitchYaw();
#if USE_SONAR || USE_BARO || USE_LIDAR_LITE
                resetAltitudeHold(&altitude);
#endif
#if USE_MAG
                resetHeadingHold(&angle);
#endif
            }
        }
#if 0
        static uint32_t loopTimer;
        while ((int32_t)(micros() - loopTimer) < 2500) {
            // Limit loop to 400 Hz
        }
        loopTimer = micros();
#endif
    }
}

// TODO:
    // Altitude hold
        // Redo take off sequence
            // Ramp up motors slowly
    // Android App
        // Self level angle trim
        // Set magnetic declination
        // Set acc_lpf_factor, gyro_cmpf_factor, gyro_cmpfm_factor, baro_noise_lpf and throttle_noise_lpf + add explanation
        // Set headMaxAngle
        // Set altHoldSetpoint and altHoldInitialThrottle for altitude hold mode
        // Control drone using virtual joystick
            // Auto take off and land in altitude hold mode
        // Show distance in graph as well
    // Add disarm timer
        // Watchdog timer as well
    // Store angles in radians as well
    // IMU driver should have MPU-6500 and HMC5883L instances, so they did not have to be in the main loop
    // Move all IMU related code into IMU driver
        // Also make generic accGyro driver
    // Use SPI for MPU-9250/6500
    // ADNS3080
        // Implement configuration: https://github.com/diydrones/ardupilot/blob/5ddbcc296dd6dd9ac9ed6316ac3134c736ae8a78/libraries/AP_OpticalFlow/AP_OpticalFlow_ADNS3080.cpp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
        // Implement "update_conversion_factors"
        // Implement 'dataReadyADNS3080'
    // LIDAR-Lite v3
        // Experiment with different configurations
        // Use seperate PID values for sonar and Lidar
    // Add RX calibration routine
        // Show live values in the app
    // Configure AUX switches via the app

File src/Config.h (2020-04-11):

/* Copyright (C) 2017 Kristian Sloth Lauszus. All rights reserved.

 This software may be distributed and modified under the terms of the GNU
 General Public License version 2 (GPL2) as published by the Free Software
 Foundation and appearing in the file GPL2.TXT included in the packaging of
 this file. Please note that GPL2 Section 2[b] requires that all works based
 on this software must also be made publicly available under the terms of
 the GPL2 ("Copyleft").

 Contact information
 -------------------

 Kristian Sloth Lauszus
 Web      :  http://www.lauszus.com
 e-mail   :  lauszus@gmail.com
*/

#ifndef __config_h__
#define __config_h__

#include <stdint.h>
#include <stdbool.h>

#include "inc/hw_ints.h"
#include "inc/hw_memmap.h"
#include "driverlib/pin_map.h"
#include "driverlib/sysctl.h"

#ifdef __cplusplus
extern "C" {
#endif

// LEDs used in various places
#define SYSCTL_PERIPH_LED               SYSCTL_PERIPH_GPIOF
#define GPIO_LED_BASE                   GPIO_PORTF_BASE
#define GPIO_RED_LED                    GPIO_PIN_1
#define GPIO_BLUE_LED                   GPIO_PIN_2
#define GPIO_GREEN_LED                  GPIO_PIN_3

// ADNS3080.c
#define GPIO_ADNS3080_RESET_PERIPH      SYSCTL_PERIPH_GPIOE
#define GPIO_ADNS3080_RESET_BASE        GPIO_PORTE_BASE
#define GPIO_ADNS3080_RESET_PIN         GPIO_PIN_1

// Bluetooth.c
#define SYSCTL_PERIPH_BLUETOOTH         SYSCTL_PERIPH_GPIOB
#define GPIO_RX_BLUETOOTH               GPIO_PB0_U1RX
#define GPIO_TX_BLUETOOTH               GPIO_PB1_U1TX
#define GPIO_BLUETOOTH_PIN_BASE         GPIO_PORTB_BASE
#define GPIO_RX_PIN_BLUETOOTH           GPIO_PIN_0
#define GPIO_TX_PIN_BLUETOOTH           GPIO_PIN_1
#define UART_NR_BLUETOOTH               1
#define UART_BASE_BLUETOOTH             UART1_BASE

// Buzzer.c
#define SYSCTL_PERIPH_BUZZER            SYSCTL_PERIPH_GPIOD
#define GPIO_BUZZER_BASE                GPIO_PORTD_BASE
#define GPIO_PIN_BUZZER                 GPIO_PIN_2

// HMC5883L.c
#define GPIO_HMC5883L_DRDY_PERIPH       SYSCTL_PERIPH_GPIOE
#define GPIO_HMC5883L_DRDY_BASE         GPIO_PORTE_BASE
#define GPIO_HMC5883L_DRDY_PIN          GPIO_PIN_3

// MPU6500.c
#define GPIO_MPU_INT_PERIPH             SYSCTL_PERIPH_GPIOE
#define GPIO_MPU_INT_BASE               GPIO_PORTE_BASE
#define GPIO_MPU_INT_PIN                GPIO_PIN_2

// PPM.c
#define SYSCTL_PERIPH_SW                SYSCTL_PERIPH_GPIOF
#define GPIO_SW_BASE                    GPIO_PORTF_BASE
#define GPIO_SW1                        GPIO_PIN_4
#define GPIO_SW2                        GPIO_PIN_0

// RX.c
// These are specific to my receiver and might need adjustment
#define RX_MIN_INPUT                    980
#define RX_MAX_INPUT                    2032

#define SYSCTL_PERIPH_RX                SYSCTL_PERIPH_GPIOC
#define GPIO_RX_BASE                    GPIO_PORTC_BASE
#define GPIO_RX                         GPIO_PIN_6

#define SYSCTL_PERIPH_RX_TIMER          SYSCTL_PERIPH_WTIMER1
#define GPIO_RX_ALTERNATE               GPIO_PC6_WT1CCP0
#define RX_TIMER_BASE                   WTIMER1_BASE
#define RX_TIMER_INT                    INT_WTIMER1A
#define RX_TIMER                        TIMER_A
#define RX_INT_FLAG                     TIMER_CAPA_EVENT
#define RX_TIMER_CFG                    TIMER_CFG_A_CAP_TIME_UP

#define SYSCTL_PERIPH_RX_LOST_TIMER     SYSCTL_PERIPH_WTIMER1
#define RX_LOST_TIMER_BASE              WTIMER1_BASE
#define RX_LOST_TIMER_INT               INT_WTIMER1B
#define RX_LOST_TIMER                   TIMER_B
#define RX_LOST_INT_FLAG                TIMER_TIMB_TIMEOUT
#define RX_LOST_TIMER_CFG               TIMER_CFG_B_PERIODIC

// Sonar.c
#define SYSCTL_PERIPH_TRIG              SYSCTL_PERIPH_GPIOE
#define GPIO_SONAR_TRIG_BASE            GPIO_PORTE_BASE
#define GPIO_SONAR_TRIG                 GPIO_PIN_0

#define SYSCTL_PERIPH_ECHO              SYSCTL_PERIPH_GPIOC
#define GPIO_SONAR_ECHO_BASE            GPIO_PORTC_BASE
#define GPIO_SONAR_ECHO                 GPIO_PIN_5

// Timer used to measure the width of the sonar echo pulse
#define SYSCTL_PERIPH_SONAR_TIMER       SYSCTL_PERIPH_WTIMER0
#define GPIO_SONAR_ALTERNATE            GPIO_PC5_WT0CCP1
#define SONAR_TIMER_BASE                WTIMER0_BASE
#define SONAR_TIMER_INT                 INT_WTIMER0B
#define SONAR_TIMER                     TIMER_B
#define SONAR_CAP_EVENT                 TIMER_CAPB_EVENT
#define SONAR_TIMER_CFG                 TIMER_CFG_B_CAP_TIME_UP

// startup_gcc.c
#define UART0_HANDLER                   UARTStdioIntHandler
#define UART1_HANDLER                   UARTStdioIntHandler1
#define UART2_HANDLER                   IntDefaultHandler
#define UART3_HANDLER                   IntDefaultHandler
#define UART4_HANDLER                   IntDefaultHandler
#define UART5_HANDLER                   IntDefaultHandler
#define UART6_HANDLER                   IntDefaultHandler
#define UART7_HANDLER                   IntDefaultHandler
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

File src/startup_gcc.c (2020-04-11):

//*****************************************************************************
//
// startup_gcc.c - Startup code for use with GNU tools.
//
// Copyright (c) 2012-2013 Texas Instruments Incorporated.  All rights reserved.
// Software License Agreement
//
// Texas Instruments (TI) is supplying this software for use solely and
// exclusively on TI's microcontroller products. The software is owned by
// TI and/or its suppliers, and is protected under applicable copyright
// laws. You may not combine this software with "viral" open-source
// software in order to form a larger program.
//
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
// This is part of revision 1.1 of the EK-TM4C123GXL Firmware Package.
//
//*****************************************************************************

#include <stdint.h>

#include "Config.h"

#include "inc/hw_nvic.h"
#include "inc/hw_types.h"

//*****************************************************************************
//
// Forward declaration of the default fault handlers.
//
//*****************************************************************************
void ResetISR(void);
static void NmiSR(void);
static void FaultISR(void);
static void IntDefaultHandler(void);

//*****************************************************************************
//
// The entry point for the application.
//
//*****************************************************************************
extern int main(void);

//*****************************************************************************
//
// External declarations for the interrupt handlers used by the application.
//
//*****************************************************************************
extern void UARTStdioIntHandler(void);
extern void UARTStdioIntHandler1(void);

//*****************************************************************************
//
// Reserve space for the system stack.
//
//*****************************************************************************
static uint32_t pui32Stack[256];

//*****************************************************************************
//
// The vector table.  Note that the proper constructs must be placed on this to
// ensure that it ends up at physical address 0x0000.0000.
//
//*****************************************************************************
__attribute__ ((section(".isr_vector")))
void (* const g_pfnVectors[])(void) =
{
    (void (*)(void))((uint32_t)pui32Stack + sizeof(pui32Stack)),
                                            // The initial stack pointer
    ResetISR,                               // The reset handler
    NmiSR,                                  // The NMI handler
    FaultISR,                               // The hard fault handler
    IntDefaultHandler,                      // The MPU fault handler
    IntDefaultHandler,                      // The bus fault handler
    IntDefaultHandler,                      // The usage fault handler
    0,                                      // Reserved
    0,                                      // Reserved
    0,                                      // Reserved
    0,                                      // Reserved
    IntDefaultHandler,                      // SVCall handler
    IntDefaultHandler,                      // Debug monitor handler
    0,                                      // Reserved
    IntDefaultHandler,                      // The PendSV handler
    IntDefaultHandler,                      // The SysTick handler
    IntDefaultHandler,                      // GPIO Port A
    IntDefaultHandler,                      // GPIO Port B
    IntDefaultHandler,                      // GPIO Port C
    IntDefaultHandler,                      // GPIO Port D
    IntDefaultHandler,                      // GPIO Port E
    UART0_HANDLER,                          // UART0 Rx and Tx
    UART1_HANDLER,                          // UART1 Rx and Tx
    IntDefaultHandler,                      // SSI0 Rx and Tx
    IntDefaultHandler,                      // I2C0 Master and Slave
    IntDefaultHandler,                      // PWM Fault
    IntDefaultHandler,                      // PWM Generator 0
    IntDefaultHandler,                      // PWM Generator 1
    IntDefaultHandler,                      // PWM Generator 2
    IntDefaultHandler,                      // Quadrature Encoder 0
    IntDefaultHandler,                      // ADC Sequence 0
    IntDefaultHandler,                      // ADC Sequence 1
    IntDefaultHandler,                      // ADC Sequence 2
    IntDefaultHandler,                      // ADC Sequence 3
    IntDefaultHandler,                      // Watchdog timer
    IntDefaultHandler,                      // Timer 0 subtimer A
    IntDefaultHandler,                      // Timer 0 subtimer B
    IntDefaultHandler,                      // Timer 1 subtimer A
    IntDefaultHandler,                      // Timer 1 subtimer B
    IntDefaultHandler,                      // Timer 2 subtimer A
    IntDefaultHandler,                      // Timer 2 subtimer B
    IntDefaultHandler,                      // Analog Comparator 0
    IntDefaultHandler,                      // Analog Comparator 1
    IntDefaultHandler,                      // Analog Comparator 2
    IntDefaultHandler,                      // System Control (PLL, OSC, BO)
    IntDefaultHandler,                      // FLASH Control
    IntDefaultHandler,                      // GPIO Port F
    IntDefaultHandler,                      // GPIO Port G
    IntDefaultHandler,                      // GPIO Port H
    UART2_HANDLER,                          // UART2 Rx and Tx
    IntDefaultHandler,                      // SSI1 Rx and Tx
    IntDefaultHandler,                      // Timer 3 subtimer A
    IntDefaultHandler,                      // Timer 3 subtimer B
    IntDefaultHandler,                      // I2C1 Master and Slave
    IntDefaultHandler,                      // Quadrature Encoder 1
    IntDefaultHandler,                      // CAN0
    IntDefaultHandler,                      // CAN1
    IntDefaultHandler,                      // CAN2
    0,                                      // Reserved
    IntDefaultHandler,                      // Hibernate
    IntDefaultHandler,                      // USB0
    IntDefaultHandler,                      // PWM Generator 3
    IntDefaultHandler,                      // uDMA Software Transfer
    IntDefaultHandler,                      // uDMA Error
    IntDefaultHandler,                      // ADC1 Sequence 0
    IntDefaultHandler,                      // ADC1 Sequence 1
    IntDefaultHandler,                      // ADC1 Sequence 2
    IntDefaultHandler,                      // ADC1 Sequence 3
    0,                                      // Reserved
    0,                                      // Reserved
    IntDefaultHandler,                      // GPIO Port J
    IntDefaultHandler,                      // GPIO Port K
    IntDefaultHandler,                      // GPIO Port L
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

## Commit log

2014-10-08 Added comment explaining why the interrupts assignments in tm4c123gh6pm.h are commented out
2014-11-09 Fixed some typos and removed extern from function prototypes
    [UART.c, main.c]
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2014-11-24 Make sure that throttle is applied
    This is just to be extra sure and will most likely be removed later on
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2014-12-11 Constrain PID output and integrated error
    [main.c]
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2014-12-11 Init PPM before anything else
    Just to make sure that motors are turned off by default
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2014-12-11 Added missing license header to PPM.c
    [PPM.c]
2014-12-11 Simplified the way incoming PID values are parsed
    Also print PID values at startup
2014-12-11 MPU-6500 values should still be read even though we are not armed in case we are in self level mode
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2014-12-11 Limit motor update rate to match ESC's (400 Hz)
    Also halved elevator and aileron control
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2014-12-12 Updated some comments and fixed whitespace
    [PPM.c, UART.c, main.c]
2014-12-12 Make sure that map doesn't produce numbers that are higher or lower than out_min and out_max
    [PPM.c]
2014-12-12 Use WTimerB as a periodic timer to shut down motors if connection to RX is lost
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2015-03-21 Turn off PPM inside interrupt handler
    This can prevent fly off in case for instance IMU connection is lost
    [RX.c]
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2015-03-21 Convert gyro readings into deg/s in main loop
    This will make it easier to work with other gyroscopes in the future
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2015-03-21 Make integrated error adjustable
    Note that 10 / 16.4 ~= 0.6
    [main.c]
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2015-03-22 Arm and disarm using rudder
    Still use AUX2 channel for safety reasons
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2015-03-23 Forgot to update Yaw PID values in UART.c as well in: d404a090fb3407d9eb8f876b4477c25224e3e506
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2015-03-23 Limit number of times that is written to the blue LED
    Also updated arm status LED, so code reflects the comment
2015-03-23 Use Kalman struct instead of having multiple Kalman files
    This will also be useful when magnetometer is implemented
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2015-03-23 Added accelerometer and ESCs calibration calls in main loop
    Also updated README
2015-03-23 Fixed bug where data got corrupted in calibrateSensor
    This must be a bug in Keil?
    [MPU6500.c]
2015-03-23 Just for extra safety the ESC calibration code needs to be manually activated in the code
2015-03-24 Use struct for accelerometer and gyro data
    Hopefully this should make the code easier to understand
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2015-03-30 Added start of Bluetooth code
    I had to make a copy of uartstdio, so it can be used with several UART interfaces
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2015-03-30 Don't set default PID values, as these are read from the EEPROM
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2015-03-30 Not going to enable tuning PID values using pots on transmitter, as this will be done using Android application
2015-03-30 Fixed bug when printing float values
    [UART.c, main.c]
2015-03-30 Prevent uartstdio send out \r before \n
    [uartstdio1.c]
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2015-03-30 Updated comment
    It is needed to send carriage return and line feed for Android application
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2015-04-02 Check number of bytes available before calling UARTPeek1, as bytes might be received after UARTPeek1 is called
    There is still a slight change that data is received between the two functions, but it is very unlikely and the checksum should prevent the data to be actually stored
    [Bluetooth.c]
2015-04-05 Moved local variables into .c file
    Also save timer load value in variable
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2015-04-17 Indicate when new values were received via Bluetooth by beeping buzzer
    [Bluetooth.c, Buzzer.c, main.c]
2015-04-17 Increase time between max and minimum PPM value fro ESC calibration and start buzzer after calibration
    Taken from: https://github.com/multiwii/multiwii-firmware/blob/952f137d98752ae48c7833cf5dc8d81af5c31227/Output.cpp#L677
    [PPM.c]
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2015-04-18 Can now calibrate accelerometer and restore default configuration values
    Nothing was changed in EEPROM.c except order of functions
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2015-04-18 Enabled OneShot125
    This allows the ESC output to be in sync with IMU reading.
    Note that motor update code was moved inside IMU reading code and some other code were rearranged - nothing else was changed in main.c
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2015-04-18 OneShot125 solved the problem with PPM being out of sync with control loop
    [main.c]
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2015-04-22 Turn on buzzer if no RX data is received
    Also cleaned up some unused code
    [Buzzer.c, RX.c]
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2015-04-23 Improved self level mode
    Use rotation matrices to rotate accelerometer vector and use LPF on accelerometer values
    Inspired by: https://github.com/cleanflight/cleanflight/blob/78a4476506c06315d7296a010a2c7ba003146b44/src/main/flight/imu.c
    Doesn't seem like I can use my Kalman filter as it is, as it written for a 1-axis application
    Note I increase optimisation level to -O3 as well, as it generated wrong code at -O0
    [Bluetooth.c, EEPROM.c, IMU.c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]
2015-04-23 Indicate when default EEPROM values are set using long beep
    Also found bug, as time needs to be initialised before buzzer
    [EEPROM.c, main.c]
2015-04-23 Added GUI application used to visualise orientation of flight controller
    For now one has to manually set: https://github.com/Lauszus/LaunchPadFlightController/blob/2555673079926c2b7602c29a05033d63cc0e9e17/src/IMU.c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 to 1.
2015-04-23 Pitch should increase when pitching forward instead, so it works well with RC elevator control input. Yaw should still increase when rotating clockwise, as that is how RC yaw control input works.
2015-04-23 Fix potential overflow bug
    [Bluetooth.c, Sonar.c]
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2015-04-24 Implement magnetometer in IMU code and added calibration routine for magnetometer
    Can also disable/enable the magnetometer code with the USE_MAG flag
2015-04-24 Fix indentation
    No new code was added
    [IMU.c]
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2015-04-24 Fix in GUI where plane were not rotated properly
    [GUI.pde]
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2015-04-25 Implemented heading hold mode
    Also found bug where angle mode were actually toggled back and forth instead of staying in angle mode
    [Bluetooth.c, EEPROM.c, UART.c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]
2015-04-28 Set accelerometer and gyroscope scale inside MPU-6500 driver
    This should make it easier to add support for other sensors in the future
2015-04-28 There is no reason to normalise magnetometer vector before calling calculateHeading, as atan only cares about the ratio between Bfx and Bfy
2015-04-28 Magnetic declination does not make sense when magnetometer is not used, so don't add it
2015-04-28 Make sure heading code is only compiled when magnetometer is actually used
    Also moved some variables into the relevant part of the code instead of being defined in the top
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2015-04-28 Heading used for heading hold wasn't reset properly to yaw angle, when motors where not running
    [main.c]
2015-05-25 Added UART handlers to vector table
    Also increased stack size to match old one in startup_rvmdk.S
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2015-05-25 UART.c no longer need "utils/ustdlib.h"
    [UART.c]
2015-05-25 Fix: warning: ISO C99 doesn't support unnamed structs/unions [-Wpedantic]
    [Bluetooth.c, HMC5883L.c, IMU.c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]
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2015-05-26 Fix plus minus symbol
    [IMU.c]
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2015-05-26 Use state machine instead of delay, so the BMP180 driver can actually be used
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2015-05-26 Check that UART_DEBUG is defined as well when running BMP180 test code
    Also renamed variable to BMP180_DEBUG instead
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2015-05-27 Use temperature from BMP180 to compensate for the difference in speed of sound in air
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2015-05-27 Check that sonar is returning valid values.
    The timer might need to be 32-bit to work, might look into it later
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2015-05-27 There is no need to reset magHold, as it is very unlikely that it will not be reset when it is first armed
    [main.c]
2015-05-27 Reset alt hold terms separately
    [EEPROM.c, main.c]
2015-05-27 There is no need to check if we should trigger sonar that often, so it is limited to the update rate of IMU
2015-05-27 Removed deadband
    It might be added to the error later
    [main.c]
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2015-05-27 Swap the two arguments in getSonarDistance, as it makes more sense that way
    [Sonar.c, main.c]
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2015-05-27 Rewrote altitude hold, so it should actually work
    The altitude set point is set every time the mode is activated. The throttle will be used in the future.
2015-05-27 Don't turn on buzzer if timer overflows in DEBUG mode
    [RX.c]
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2015-05-28 Fix bug where initial throttle were not set properly because of type (-0.95f should have been -95.0f)
    Min and max check value where moved inside RX.h, to prevent it from happening again
    [main.c]
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2015-05-29 Altitude hold wan't properly reset
    [main.c]
2015-05-29 Turn on buzzer if sonar is returning an error, as this should never happen
    This is most likely caused by a loose write
    [main.c]
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2015-05-30 Fix so Bluetooth code compiles when no magnetometer is used
    [Bluetooth.c, main.c]
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2015-05-30 Surrond uartstdio.h include in if statements, so it throws an error if one try to print anyway
    [AltitudeHold.c, BMP180.c, Bluetooth.c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]
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2015-06-08 No need to reset stateTimer in state 3
    [Logger.c]
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2015-06-17 Disabled UART by default and moved pro processor directives up to the top of Makefile
    Also fixed description for flash rule
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2015-06-18 Fixed comments and variable names as it is in the body frame and the altitude estimation should rotate it back into the inertial frame
    [AltitudeHold.c, IMU.c]
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2015-06-18 Fixed compile error when compiling with USE_MAG=0
    [IMU.c]
2015-06-18 Yaw angle is already inverted
    [AltitudeHold.c]
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2015-06-26 Uploaded final report
    [10x4.7-clockwise-propeller.0002.ipt, 10x4.7-clockwise-propeller.SLDPRT, 10x4.7-clockwise-propeller.ipt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]
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2015-07-29 Fixed typo in BMP180 driver
    [AltitudeHold.c, BMP180.c]
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2015-07-29 Turn on buzzer in case AK8963 overflows
    [AK8963.c]
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2015-07-29 Fixed debug print
2015-07-29 Cast sensor data explicitly to int16_t
    This was causing issues in the calibrateSensor function on some compilers, it was just done in the rest of the code to be future proof
    [AK8963.c, HMC5883L.c, MPU6500.c]
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2015-07-29 Stay in endless while loop if HMC5883L is detected, but self test fails
    [HMC5883L.c]
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2015-08-21 Uploaded PCB files
    Can be ordered here: https://oshpark.com/profiles/Lauszus
    [LaunchPadFlightController_Schematic.brd, LaunchPadFlightController_Schematic.sch]
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2015-09-07 Fix orientation of MPU-9250/6500 and HMC5883L, so they corresponds with the PCB
    [HMC5883L.c, MPU6500.c]
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2016-01-18 Fixed a bunch of warnings
    [ADNS3080.c]
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2017-01-13 Do not use the mode control pin, as we would be polling it anyway
    It is always very noise and will require a 1k pull-down and a 1 pF capacitor to GND
    [LidarLiteV3.c, main.c]
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2017-03-15 Subtract 1g before the z-acceleration is inverted
    [AltitudeHold.c]
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2017-03-19 Added missing shabang in Python script
    [ADNS3080ImageGrabber.py]
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2017-04-10 Since the accelerometer readings from the MPU-6500 are inverted, we need to invert the zero values as well
    This bug was introduced in: 9f6ec76b513da1b92a2425234e9824c2bbe320df
    [EEPROM.c, MPU6500.c]
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2017-05-12 Fixed name of UART number and UART base defines
    [Bluetooth.c, Config.h, UART.c]
2017-05-28 Do not invert the accelerometer axis inside the MPU-driver, as then the altitude is not calculated correctly
    [AltitudeHold.c, EEPROM.c, IMU.c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]
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
